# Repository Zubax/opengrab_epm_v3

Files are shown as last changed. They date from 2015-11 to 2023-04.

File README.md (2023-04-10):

OpenGrab EPM v3
===============

⚠⚠ **OpenGrab EPM v3 is no longer in production. Please use [Zubax EPM](https://zubax.com/products/epm) as a replacement.** ⚠⚠

-----

OpenGrab EPM v3 is an electropermanent magnet, combining the advantages of electro and permanent magnets.
It has been developed by [NicaDrone](http://nicadrone.com) in collaboration with [Zubax Robotics](http://zubax.com).

Useful links:

* [**PRODUCT DOCUMENTATION**](https://kb.zubax.com/x/eoAh)
* [HARDWARE SOURCES](https://tools.upverter.com/eda/#designId=1dada3422c772add)
* [SUPPORT FORUM](http://forum.zubax.com)

## Building the firmware

### Prerequisites

* Python 2.7+ or Python 3.2+
* ARM GCC Embedded 4.9+

### Building

After cloning this repository, execute the following:

```bash
git submodule update --init --recursive
cd firmware
make -j8
```

The build outputs will be available in the directory `build/`.

## Flashing the firmware

### Useful info

* If you do not cycle the EPM you cannot get zapped.
* Don't zap your computer it will not survive.
* HV section to avoid touching during debug, see fig. 1.
* Solder Jumper settings see fig. 1 and 2.

#### V3 Rev 4B and earlier
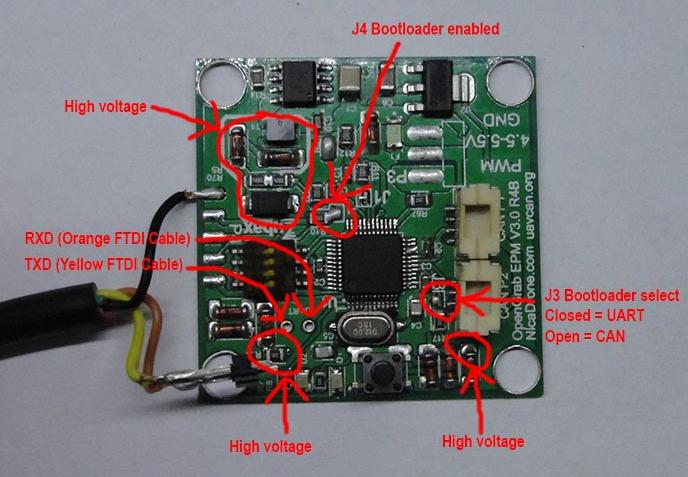
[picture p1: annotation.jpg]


#### V3 Rev 5C
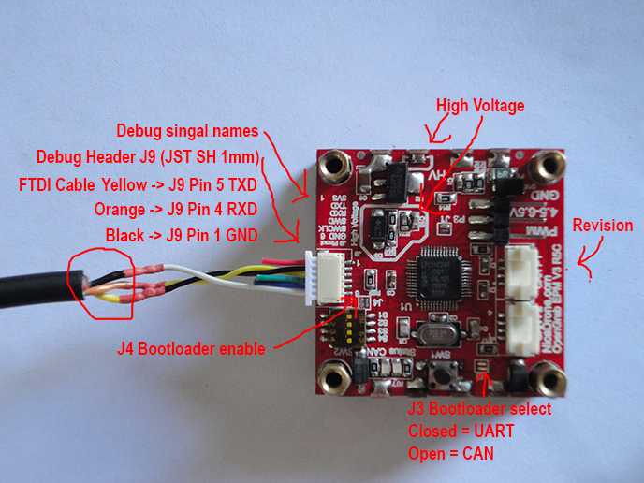
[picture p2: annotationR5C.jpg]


### Via UART

#### Connecting USB-UART adapter

FTDI cable is the recommended USB-UART adapter.
5 V and 3.3 V FTDI cables work fine, 3.3 V is recommended.
Use the following pinout when connecting:

Wire    | Signal
--------|--------
Orange  | RXD
Yellow  | TXD
Black   | GND

#### Flashing with NXP Flash Magic (simplest method)

Get the flashing tool from <http://www.flashmagictool.com/>.
Start the tool, then configure it as follows:

Parameter       | Value
----------------|------------------------------------
Select Device   | LPC11C24/301
Baud rate       | 115200
Interface       | ISP
Oscilator       | 12 MHz
File            | Prebuilt `.hex` available [here](https://files.zubax.com/products/com.zubax.opengrab_epm_v3/) **

1. Connect the USB-UART adapter.
2. Close J3 to select serial bootloader.
3. Close J4 to force the LPC to start the bootloader.
4. Power up the board.
5. Run the flashing tool.

** `.hex` is also created in the build output directory `firmware/build` or a `.hex` file can be created from `.bin`:

```bash
arm-none-eabi-objcopy -I binary -O ihex firmware.bin out.hex
```

### Via DroneCode Probe

[DroneCode Probe](https://kb.zubax.com/x/iIAh) is a generic JTAG / SWD + UART console adapter
compatible with most ARM Cortex based designs and in particular with hardware maintained by the
[DroneCode project](http://dronecode.org).

In order to flash the board using this tool, simply connect the debugger and execute the script
`blackmagic_flash.sh`.

### Via [8devices USB2CAN](http://www.8devices.com/usb2can) and embedded CAN bootloader

Note to Windows users: In order to use USB2CAN in a VM the drivers have to be installed on the host and driver
signature enforcement has to be disabled in some versions of Windows.

Register the CAN interface with SocketCAN:

```bash
sudo ip link set can0 up type can bitrate 100000 sample-point 0.875
```

Uploading binary using LPC11 embedded CAN bootloader:

```bash
tools/drwatson/lpc11c00_can_bootloader.py can0 firmware/build/firmware.bin
```

## Licenses

### Firmware

Copyright (C) 2015  Zubax Robotics <info@zubax.com>

This program is free software: you can redistribute it and/or modify
it under the terms of the GNU General Public License as published by
the Free Software Foundation, either version 3 of the License, or
(at your option) any later version.

This program is distributed in the hope that it will be useful,
but WITHOUT ANY WARRANTY; without even the implied warranty of
MERCHANTABILITY or FITNESS FOR A PARTICULAR PURPOSE.  See the
GNU General Public License for more details.

You should have received a copy of the GNU General Public License
along with this program.  If not, see <http://www.gnu.org/licenses/>.

### Hardware

The hardware sources are distributed under the terms of
[CC BY-SA 4.0](https://creativecommons.org/licenses/by-sa/4.0/).

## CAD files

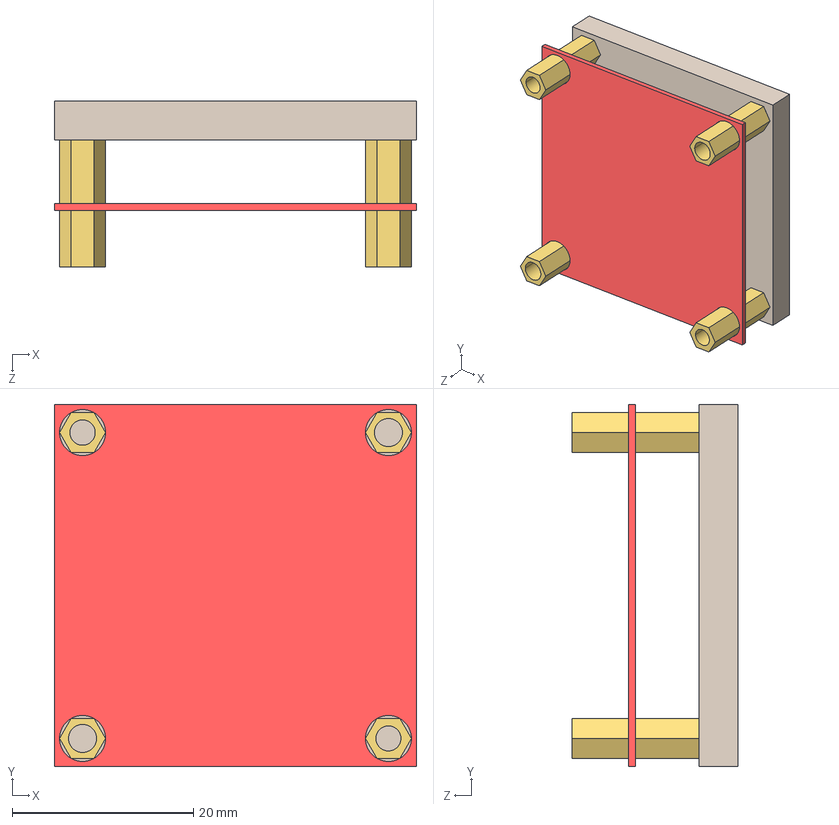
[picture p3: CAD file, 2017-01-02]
hardware/EPM_V3_Model.STEP
40.0 x 40.0 x 18.3 mm

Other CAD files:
hardware/EPM_V3_Model.IGS
hardware/EPM_V3_Model.SLDPRT

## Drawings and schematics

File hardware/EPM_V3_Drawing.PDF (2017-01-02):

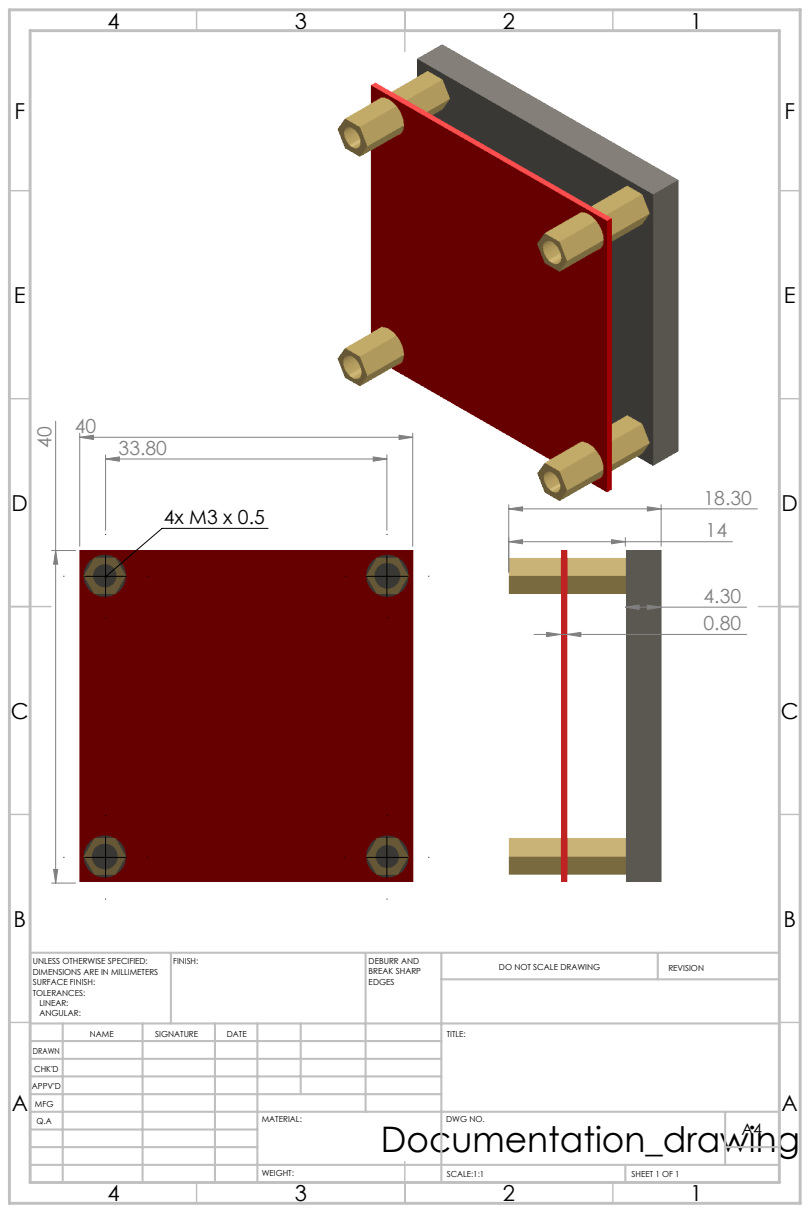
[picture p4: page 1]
FINISH:; DEBURR AND; BREAK SHARP; DO NOT SCALE DRAWING; REVISION; SCALE:1:1; SHEET 1 OF 1

UNLESS OTHERWISE SPECIFIED:
DIMENSIONS ARE IN MILLIMETERS
SURFACE FINISH:
TOLERANCES:
LINEAR:
ANGULAR:

NAME | SIGNATURE | DATE | | | | TITLE:

DRAWN
CHK'D
APPV'D
MFG
Q.A | | | | MATERIAL: Documentation_drawing | DWG NO. | A4

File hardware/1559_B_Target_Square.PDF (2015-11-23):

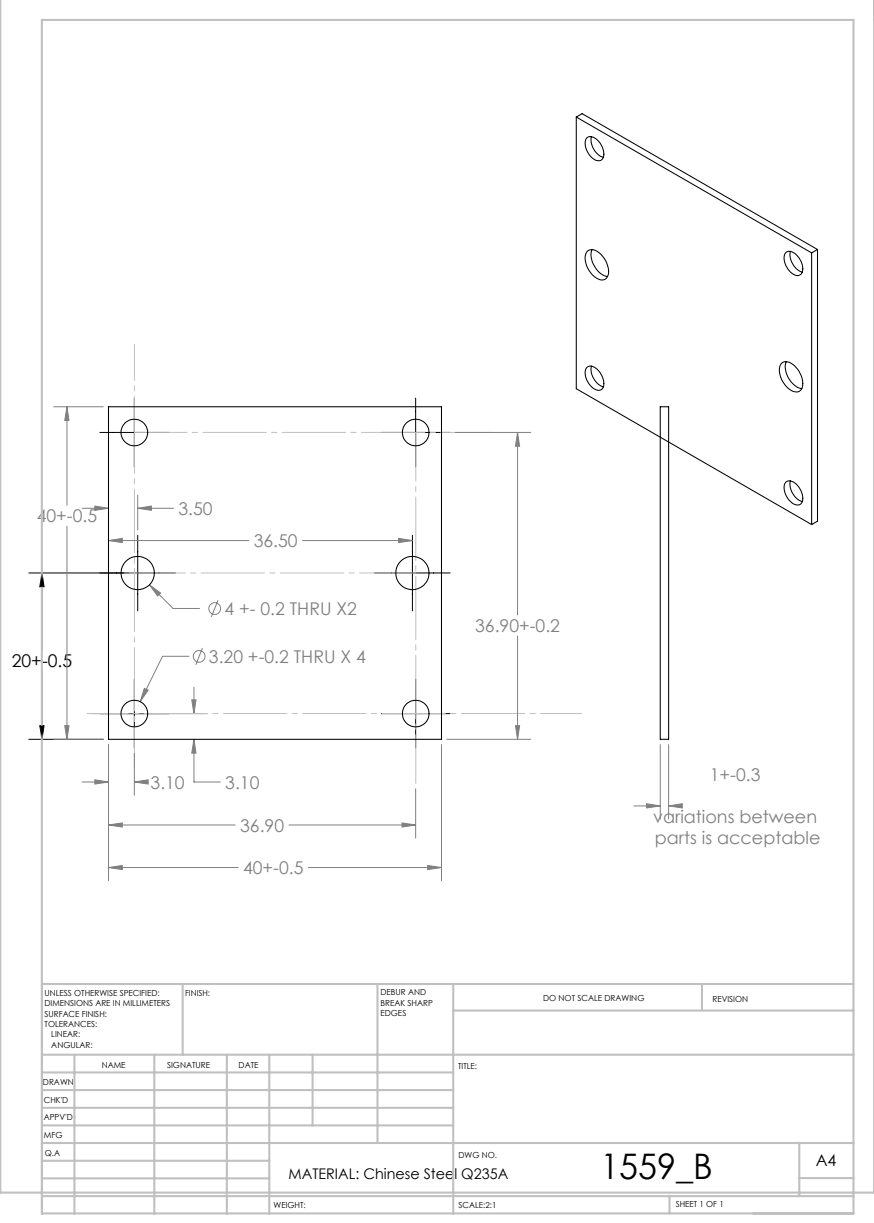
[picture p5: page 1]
3.20 +-0.2 THRU X 4; 4 +- 0.2 THRU X2; SCALE:2:1; SHEET 1 OF 1; DO NOT SCALE DRAWING; REVISION; DEBUR AND BREAK SHARP; UNLESS OTHERWISE SPECIFIED:; FINISH:

variations between
parts is acceptable

DIMENSIONS ARE IN MILLIMETERS
SURFACE FINISH:
TOLERANCES:
LINEAR:
ANGULAR:

NAME | SIGNATURE | DATE | | | | TITLE:

DRAWN
CHK'D
APPV'D
MFG
Q.A | | | | MATERIAL: Chinese Steel Q235A | 1559_B WEIGHT: DWG NO. | A4

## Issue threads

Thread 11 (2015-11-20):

Funky behavior when UAVCAN and PWM or button is used at the same time

ctech4285, 2015-11-20:
Temporary fix: Don't use CAN and PWM together,

PWM should be ignored when CAN is being used.

The CAN command is being send over and over again and the receiver only response to a change in command.
This is the typical way to use CAN bus - the same state is being published at a fixed rate or when it changes
This allows to ensure consistency even if the receiving node restarts

There seems to be a bug in somewhere as well....

pavel-kirienko, 2016-02-01:
Closing because we've already discussed that the device cannot accept multiple contradictory inputs at the same time.

Closed 2016-02-01.

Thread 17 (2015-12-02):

Command rate limiting not working when going on->off->on->off.....

ctech4285, 2015-12-02:

pavel-kirienko, 2015-12-02:
I understood that rate limiting is only needed if the goal does not change.

Remove `magnet_is_on` condition from https://github.com/Zubax/opengrab_epm_v3/blob/master/firmware/src/magnet/magnet.cpp#L194 and https://github.com/Zubax/opengrab_epm_v3/blob/master/firmware/src/magnet/magnet.cpp#L213

pavel-kirienko, 2015-12-03:
Is it fixed now?

ctech4285, 2015-12-03:
I can see now why you did it this way. Now a user has to wait like 3 seconds before going from turn on -> turn off...
Let me see what I can cock up

pavel-kirienko, 2016-02-01:
Still relevant?

Closed 2016-02-01.

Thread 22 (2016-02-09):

Vin measurement incorrect after boot

ctech4285, 2016-02-09:
make PRODROPPER=1

First time after boot when Vin is measured it returns 5000ish mV instead of 12000ish. ACD pin V is correct at this time at around 1000mV.

This commit has the syslog print out to reproduce

https://github.com/Zubax/opengrab_epm_v3/tree/pro_epm

pavel-kirienko, 2016-02-09:
This is because of averaging: https://github.com/Zubax/opengrab_epm_v3/blob/master/firmware/src/sys/board.cpp#L471.

We can either add initialization of the previous sample on first measurement, or we can remove averaging completely. We probably should remove it, it's wonky.

ctech4285, 2016-02-09:
Let's leave it in and call getSupplyVoltageInMillivolts a few times after boot? I am worried about introducing sporadic noise

pavel-kirienko, 2016-02-09:
No, we must not call it multiple times after boot because that creates a leaky abstraction. We can do this, right after `x` is computed:

```c++
if (old_value == 0)  // If old value is uninitialized, the result will be half of the real value
{
    x *= 2;
}
```

Closed 2016-02-11.

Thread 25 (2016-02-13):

Migrate to JST GH

pavel-kirienko, 2016-02-13:
References:
- http://www.digikey.com/product-detail/en/SM04B-GHS-TB(LF)(SN)%3B-/455-1566-1-ND/807834
- http://uavcan.org/Specification/8._Hardware_design_recommendations/#physical-connector-definition
- https://github.com/PX4/Hardware/issues/18

ctech4285, 2016-02-13:
This is going into PCB Rev6 then

ctech4285, 2016-11-07:
Done

Closed 2016-11-07.

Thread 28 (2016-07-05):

Customer was able to kill his EPM when turning on constantly

ctech4285, 2016-07-05:
There are some variations on the saturation current of T1 between parts

Reevalute using a smaller PTC fuse, fuse should pop before T1 gets damaged

Increasing minimum command interval

ctech4285, 2016-08-04:
cleaner implementation of better cycle limiting addressed this #34

Closed 2016-08-04.

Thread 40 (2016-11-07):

ADC seems to hickup every now and then

ctech4285, 2016-11-07:
It seems that it miss read input or output voltage, triggers an error

pavel-kirienko, 2016-11-07:
Please provide more info; the description you provided is insufficient. How exactly the misreading happens? How frequently? What output is produced and what output is expected? What error is triggered?

ctech4285, 2016-11-08:
Problem found, external ADC capacitor lags behind the main capacitor voltage.

https://github.com/Zubax/opengrab_epm_v3/blob/master/firmware/src/magnet/magnet.cpp#L262

Closed 2016-11-08.

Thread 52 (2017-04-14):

Catastrophic failure mode possible on different hardware

ctech4285, 2017-04-14:
Force 1 second delay when power stage misfires. Misfire = main capacitor is not  discharged after firing

It is possible on different hardware that the holding current is reached. Via the cathode pull down resistor on the power stage
It cause the Thyristor to stay on for up to 1 second. Subsequently firing its lower pair will cause the two thyristors to eat to much power and fail as short.

I'll take care of it before we change out the thyristors for the next rev

pavel-kirienko, 2017-04-22:
Please keep us posted. Let me know if any software changes are necessary.

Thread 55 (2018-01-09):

J9 Pin numbers in documentation pictures are incorrect

ctech4285, 2018-01-09:
https://github.com/Zubax/opengrab_epm_v3/raw/master/annotationR5C.jpg

Pin numbers on the PCB are correct; Pin number on the picture are incorrect

ctech4285, 2018-02-05:
User reports silkscreen label or the documentation is wrong. Pins 1-6 on J9 are labelled in the wrong order.

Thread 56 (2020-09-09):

Link to the hardware sources is broken.

nophead, 2020-09-09:
The title says it all.

pavel-kirienko, 2020-09-09:
@ctech4285 do we have any hope of fixing it?

nophead, 2020-09-10:
Is there any other source for the component positions. I want to 3D print an enclosure, so I need to know where the connectors, button, LEDs and switches are located.

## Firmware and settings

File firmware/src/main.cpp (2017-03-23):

/*
 * OpenGrab EPM - Electropermanent Magnet
 * Copyright (C) 2015  Zubax Robotics <info@zubax.com>
 *
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
 * Author: Pavel Kirienko <pavel.kirienko@zubax.com>
 *         Andreas Jochum <andreas@nicadrone.com>
 */

#include <cstdio>
#include <algorithm>
#include <sys/board.hpp>
#include <uavcan_lpc11c24/uavcan_lpc11c24.hpp>
#include <uavcan/equipment/hardpoint/Command.hpp>
#include <uavcan/equipment/hardpoint/Status.hpp>
#include <uavcan/protocol/dynamic_node_id_client.hpp>
#include <magnet/magnet.hpp>

namespace
{

static constexpr unsigned NodeMemoryPoolSize = 2800;

uavcan::Node<NodeMemoryPoolSize>& getNode()
{
    static uavcan::Node<NodeMemoryPoolSize> node(uavcan_lpc11c24::CanDriver::instance(),
                                                 uavcan_lpc11c24::SystemClock::instance());
    return node;
}

struct HwConfig
{
    std::uint8_t hardpoint_id = 0;
    bool use_hardpoint_id_as_node_id = false;

    static constexpr std::uint8_t NodeIDOffset = 100;
};

const HwConfig getHwConfig()
{
    static bool first = true;
    static HwConfig cfg;

    if (first)
    {
        first = false;
        const auto x = board::readDipSwitch();
        cfg.hardpoint_id = x & ((1 << (board::DipSwitchBits - 1)) - 1);
        cfg.use_hardpoint_id_as_node_id = (x >> (board::DipSwitchBits - 1)) != 0;
    }

    return cfg;
}

void callPollAndResetWatchdog()
{
    board::resetWatchdog();

    /*
     * Status LED update
     */
    const auto ts = board::clock::getMonotonic();

    static board::MonotonicTime led_update_deadline = ts;
    static bool led_status = false;
    static bool boot = true;
    static bool first_time_led_update = true;

    /*
     * LED DIP test after boot
     */
    if (boot)
    {
        boot = !boot;
        if(board::readDipSwitch() == 0)
        {
            board::setStatusLed(true);
            board::setCanLed(true);
            led_update_deadline += board::MonotonicDuration::fromMSec(500);
        }
    }

    if (ts >= led_update_deadline)
    {
        if(first_time_led_update)           // Turn off CAN status
        {
            board::setCanLed(false);
            first_time_led_update = !first_time_led_update;
        }
        led_status = !led_status;
        board::setStatusLed(led_status);

        if (led_status)
        {
            led_update_deadline += board::MonotonicDuration::fromMSec(50);
        }
        else
        {
            led_update_deadline += board::MonotonicDuration::fromMSec(
                (magnet::getHealth() == magnet::Health::Ok)      ? 950 :
                (magnet::getHealth() == magnet::Health::Warning) ? 500 : 100);
        }

        /* Debug
         * board::syslog("Vin = ", board::getSupplyVoltageInMillivolts(), " mV\r\n");
         * board::syslog("Vout = ", board::getOutVoltageInVolts(), " V\r\n");
         */
    }

    /*
     * PWM control update
     */
    const auto pwm = board::getPwmInput();
    if (pwm != board::PwmInput::NoSignal &&
        pwm != board::PwmInput::Neutral)
    {
        if (pwm == board::PwmInput::High)
        {
            magnet::turnOn(magnet::MinTurnOnCycles);
        }
        if (pwm == board::PwmInput::Low)
        {
            magnet::turnOff();
        }
    }

    /*
     * Button update
     */
    if (board::hadButtonPressEvent() || board::hadExternalButtonPressEvent() )
    {
        if (magnet::isTurnedOn())
        {
            magnet::turnOff();
        }
        else
        {
            magnet::turnOn(magnet::MinTurnOnCycles);
        }
    }

    /*
     * Magnet update
     */
    magnet::poll();
}

uavcan::NodeID performDynamicNodeIDAllocation()
{
    uavcan::DynamicNodeIDClient client(getNode());

    const int client_start_res = client.start(getNode().getHardwareVersion().unique_id);
    if (client_start_res < 0)
    {
        board::die();
    }

    while (!client.isAllocationComplete())
    {
        (void)getNode().spinOnce();
        callPollAndResetWatchdog();
    }

    return client.getAllocatedNodeID();
}

void fillNodeInfo()
{
    getNode().setName("com.zubax.opengrab_epm_v3");

    {
        uavcan::protocol::SoftwareVersion swver;

        swver.major = FW_VERSION_MAJOR;
        swver.minor = FW_VERSION_MINOR;
        swver.vcs_commit = GIT_HASH;
        swver.optional_field_flags = swver.OPTIONAL_FIELD_FLAG_VCS_COMMIT;

        getNode().setSoftwareVersion(swver);
    }

    {
        uavcan::protocol::HardwareVersion hwver;

        hwver.major = HW_VERSION_MAJOR;

        {
            board::UniqueID uid;
            board::readUniqueID(uid);
            std::copy(std::begin(uid), std::end(uid), std::begin(hwver.unique_id));
        }

        {
            board::DeviceSignature coa;
            if (board::tryReadDeviceSignature(coa))
            {
                std::copy(std::begin(coa), std::end(coa), std::back_inserter(hwver.certificate_of_authenticity));
            }
        }

        getNode().setHardwareVersion(hwver);
    }
}

void configureAcceptanceFilters()
{
    // These masks are specific for UAVCAN - we're using only extended data frames and nothing else.
    static constexpr auto CommonIDBits   = uavcan::CanFrame::FlagEFF;
    static constexpr auto CommonMaskBits = uavcan::CanFrame::FlagEFF |
                                           uavcan::CanFrame::FlagRTR |
                                           uavcan::CanFrame::FlagERR;

    static constexpr auto NodeIDShift     = 8;
    static constexpr auto MessageMaskBits = 0xFFFF80U;
    static constexpr auto ServiceIDBits   = 0x80U;
    static constexpr auto ServiceMaskBits = 0x7F80U;

    // Allocating a buffer large enough to fit all filters the application may need.
    static constexpr unsigned MaxFilterConfigs = 32;
    uavcan::CanFilterConfig filter_configs[MaxFilterConfigs];
    std::uint16_t filter_config_index = 0;

    // Building message filters.
    auto p = getNode().getDispatcher().getListOfMessageListeners().get();
    while (p != NULL)
    {
        filter_configs[filter_config_index].id =
            (static_cast<unsigned>(p->getDataTypeDescriptor().getID().get()) << NodeIDShift) | CommonIDBits;

        filter_configs[filter_config_index].mask = MessageMaskBits | CommonMaskBits;

        p = p->getNextListNode();

        filter_config_index++;
        if (filter_config_index >= std::min<unsigned>(MaxFilterConfigs,
                                                      uavcan_lpc11c24::CanDriver::instance().getNumFilters()))
        {
            board::die(); // Filter compaction algorithm defined in libuavcan is not used because of memory constraints
        }
    }

    // Adding one filter for unicast transfers - note that it's filtering on our Node ID.
    filter_configs[filter_config_index].id =
        ServiceIDBits | (static_cast<unsigned>(getNode().getNodeID().get()) << NodeIDShift) | CommonIDBits;
    filter_configs[filter_config_index].mask = ServiceMaskBits | CommonMaskBits;

    filter_config_index++;

    // Sending the configuration to the CAN driver.
    if (uavcan_lpc11c24::CanDriver::instance().configureFilters(filter_configs, filter_config_index) < 0)
    {
        board::die();
    }
}

void handleHardpointCommand(const uavcan::equipment::hardpoint::Command& msg)
{
    if (msg.hardpoint_id != getHwConfig().hardpoint_id)
    {
        return;
    }

    /*
     * The last command field is initialized at an impossible value in order to force a switch once
     * the first command is received. This will force the magnet into a known state.
     */
    static unsigned last_command = std::numeric_limits<unsigned>::max();

    if ((bool(msg.command) != magnet::isTurnedOn()) || (msg.command != last_command))
    {
        if (msg.command == 0)
        {
            magnet::turnOff();
        }
        else
        {
            magnet::turnOn(msg.command);
        }
    }

    // Oi moroz moroz ne moroz' mena
    last_command = msg.command; // Ne moroz' mena moigo kona
}

void publishHardpointStatus()
{
    static const auto Priority = uavcan::TransferPriority::MiddleLower;

    static uavcan::Publisher<uavcan::equipment::hardpoint::Status> pub(getNode());

    static bool initialized = false;
    if (!initialized)
    {
        initialized = true;
        pub.setPriority(Priority);
    }

    uavcan::equipment::hardpoint::Status msg;

    msg.hardpoint_id = getHwConfig().hardpoint_id;

    msg.payload_weight = std::numeric_limits<float>::quiet_NaN();
    msg.payload_weight_variance = std::numeric_limits<float>::infinity();

    msg.status = magnet::isTurnedOn() ? 1 : 0;

    (void)pub.broadcast(msg);
}

void updateUavcanStatus(const uavcan::TimerEvent&)
{
    publishHardpointStatus();

    switch (magnet::getHealth())
    {
    case magnet::Health::Ok:
    {
        getNode().setHealthOk();
        break;
    }
    case magnet::Health::Warning:
    {
        getNode().setHealthWarning();
        break;
    }
    default:
    {
        getNode().setHealthError();
        break;
    }
    }

    getNode().setVendorSpecificStatusCode(
        static_cast<std::uint16_t>(magnet::getStatusFlags() | ((board::getOutVoltageInVolts() >> 1) << 8)));
}

void updateCanLed(const uavcan::TimerEvent&)
{
    board::setCanLed(uavcan_lpc11c24::CanDriver::instance().hadActivity());
}

#if __GNUC__
__attribute__((noinline))
#endif
void init()
{
    board::syslog("Boot\r\n");
    board::syslog("FW built at ");
    board::syslog(__DATE__);
    board::syslog("\r\n");
    board::resetWatchdog();

    callPollAndResetWatchdog();

    /*
     * Configuring the CAN controller
     */
    std::uint32_t bit_rate = 0;
    while (bit_rate == 0)
    {
        bit_rate = uavcan_lpc11c24::CanDriver::detectBitRate(&callPollAndResetWatchdog);
    }
    board::syslog("Bitrate: ", bit_rate, "\r\n");

    if (uavcan_lpc11c24::CanDriver::instance().init(bit_rate) < 0)
    {
        board::die();
    }

    board::syslog("CAN init ok\r\n");

    callPollAndResetWatchdog();

    /*
     * Starting the node
     */
    fillNodeInfo();

    if (getNode().start() < 0)
    {
        board::die();
    }

    callPollAndResetWatchdog();

    /*
     * Starting the node and performing dynamic node ID allocation
     */
    if (getNode().start() < 0)
    {
        board::die();
    }

    /*
     * Initializing other libuavcan-related objects
     * Why reinterpret_cast<>() on function pointers? Try to remove it, or replace with static_cast. GCC is fun.   D:
     */
    static uavcan::TimerEventForwarder<void (*)(const uavcan::TimerEvent&)> can_led_timer(getNode());   // CAN LED tmr
    can_led_timer.setCallback(reinterpret_cast<decltype(can_led_timer)::Callback>(&updateCanLed));
    can_led_timer.startPeriodic(uavcan::MonotonicDuration::fromMSec(25));

    if (getHwConfig().use_hardpoint_id_as_node_id)
    {
        board::syslog("Node ID is fixed\r\n");
        getNode().setNodeID(static_cast<std::uint8_t>(getHwConfig().hardpoint_id + HwConfig::NodeIDOffset));
    }
    else
    {
        board::syslog("Node ID allocation...\r\n");
        getNode().setNodeID(performDynamicNodeIDAllocation());
    }

    board::syslog("Node ID ", getNode().getNodeID().get(), "\r\n");

    callPollAndResetWatchdog();

    /*
     * Initializing other libuavcan-related objects
     */
    static uavcan::TimerEventForwarder<void (*)(const uavcan::TimerEvent&)> update_timer(getNode());    // Status pub
    update_timer.setCallback(reinterpret_cast<decltype(update_timer)::Callback>(&updateUavcanStatus));
    update_timer.startPeriodic(uavcan::MonotonicDuration::fromMSec(500));

    static uavcan::Subscriber<uavcan::equipment::hardpoint::Command,                                    // Command sub
                              void (*)(const uavcan::equipment::hardpoint::Command&)> command_sub(getNode());
    if (command_sub.start(reinterpret_cast<decltype(command_sub)::Callback>(&handleHardpointCommand)) < 0)
    {
        board::die();
    }

    /*
     * Configuring the filters in the last order, when all subscribers are initialized.
     */
    configureAcceptanceFilters();
}

}

int main()
{
    init();

    getNode().setModeOperational();

    board::setStatusLed(false);

    board::syslog("Init OK\r\n");

    while (true)
    {
        const int res = getNode().spinOnce();
        if (res < 0)
        {
            board::syslog("Spin error ", res, "\r\n");
        }

        callPollAndResetWatchdog();
    }
}

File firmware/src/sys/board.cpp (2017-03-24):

/*
 * OpenGrab EPM - Electropermanent Magnet
 * Copyright (C) 2015  Zubax Robotics <info@zubax.com>
 *
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
 * Author: Pavel Kirienko <pavel.kirienko@zubax.com>
 *         Andreas Jochum <andreas@nicadrone.com>
 *
 * Board initialization for Olimex LPC11C24 and EPM hardware.
 */

#include "board.hpp"
#include <chip.h>
#include <cstdlib>
#include <cstring>
#include <numeric>
#include <cstdint>
#include <algorithm>
#include <array>
#include <uavcan_lpc11c24/clock.hpp>

#define PDRUNCFGUSEMASK 0x0000ED00
#define PDRUNCFGMASKTMP 0x000000FF

constexpr std::uint32_t OscRateIn = 12000000; ///< External crystal
constexpr std::uint32_t ExtRateIn = 0;

std::uint32_t SystemCoreClock = 12000000; ///< Initialized to default clock value, will be changed on init

namespace board
{
namespace
{

constexpr std::uint32_t TargetSystemCoreClock = 48000000;

constexpr unsigned AdcReferenceMillivolts = 3300;
constexpr unsigned AdcResolutionBits = 10;

constexpr unsigned PwmPortNum = 2;
constexpr unsigned PwmInputPinMask = 1U << 10;

#if BOARD_OLIMEX_LPC_P11C24
constexpr unsigned CanLedPortNum = 1;
constexpr unsigned CanLedPinMask = 1U << 11;
#else
constexpr unsigned CanLedPortNum = 2;
constexpr unsigned CanLedPinMask = 1U << 6;
#endif

constexpr unsigned StatusLedPortNum = 2;
constexpr unsigned StatusLedPinMask = 1U << 0;

constexpr unsigned ExternalButtonPortNum = 1;
constexpr unsigned ExternalButtonPinMask = 1U << 6;

constexpr unsigned PumpSwitchPortNum = 1;
constexpr unsigned PumpSwitchPinMask = (1U << 0) | (1U << 1) | (1U << 2) | (1U << 4);

constexpr unsigned MagnetCtrlPortNum = 2;

constexpr unsigned MagnetCtrlPinLeftLow   = 1U << 2;   // PIO2_2
constexpr unsigned MagnetCtrlPinRightHigh = 1U << 8;   // PIO2_8

constexpr unsigned MagnetCtrlPinRightLow  = 1U << 1;   // PIO2_1
constexpr unsigned MagnetCtrlPinLeftHigh  = 1U << 7;   // PIO2_7

constexpr unsigned DipSwitchPortNum = 3;
constexpr unsigned DipSwitchPinMask = 0b1111;

constexpr std::uint32_t PwmInputPeriodMinUSec = 500;
constexpr std::uint32_t PwmInputPeriodMaxUSec = 2500;
constexpr std::uint32_t PwmInputTimeoutUSec   = 100000;
static std::uint32_t pwm_input_pulse_usec;
static uavcan::MonotonicTime last_pwm_input_update_ts;

struct CriticalSectionLocker
{
    CriticalSectionLocker()
    {
        __disable_irq();
    }
    ~CriticalSectionLocker()
    {
        __enable_irq();
    }
};

struct PinMuxGroup
{
    const unsigned pin      : 8;
    const unsigned modefunc : 24;
};

/**
 * Note that output pins that must be initialized with low output level are configured with PULLDOWN.
 * This is a work around - the GPIO controller does not provide a deterministic way to set initial output value;
 * instead, once the DIR bit goes up, the output state will be determined by the input state at the moment when the
 * DIR bit was changed.
 * Refer to the chapter "12.3.1 GPIO data register" of the user manual for details.
 */
constexpr PinMuxGroup pinmux[] =
{
    // PIO0
    { IOCON_PIO0_11, IOCON_FUNC2 | IOCON_MODE_INACT | IOCON_ADMODE_EN |IOCON_OPENDRAIN_EN },    // Vout_ADC

    // PIO1
    { IOCON_PIO1_10, IOCON_FUNC1 | IOCON_MODE_INACT | IOCON_ADMODE_EN |IOCON_OPENDRAIN_EN },    // Vin_ADC

    { IOCON_PIO1_7,  IOCON_FUNC1 | IOCON_HYS_EN | IOCON_MODE_PULLUP },                          // UART_TXD
#if BOARD_OLIMEX_LPC_P11C24
    { IOCON_PIO1_11, IOCON_FUNC0 | IOCON_HYS_EN | IOCON_DIGMODE_EN },                           // CAN LED
#endif

    { IOCON_PIO1_0,  IOCON_FUNC1 | IOCON_MODE_PULLDOWN | IOCON_HYS_EN | IOCON_DIGMODE_EN },     // PUMP SW0
    { IOCON_PIO1_1,  IOCON_FUNC1 | IOCON_MODE_PULLDOWN | IOCON_HYS_EN | IOCON_DIGMODE_EN },     // PUMP SW1
    { IOCON_PIO1_2,  IOCON_FUNC1 | IOCON_MODE_PULLDOWN | IOCON_HYS_EN | IOCON_DIGMODE_EN },     // PUMP SW2
    { IOCON_PIO1_4,  IOCON_FUNC0 | IOCON_MODE_PULLDOWN | IOCON_HYS_EN | IOCON_DIGMODE_EN },     // PUMP SW4
    { IOCON_PIO1_6,  IOCON_FUNC0 | IOCON_HYS_EN | IOCON_MODE_PULLDOWN },                        // External Button

    // PIO2
    { IOCON_PIO2_0,  IOCON_FUNC0 | IOCON_HYS_EN | IOCON_MODE_PULLDOWN },                        // Status LED
#if !BOARD_OLIMEX_LPC_P11C24
    { IOCON_PIO2_6,  IOCON_FUNC0 },                                                             // CAN LED
#endif

    { IOCON_PIO2_10, IOCON_FUNC0 | IOCON_HYS_EN | IOCON_MODE_PULLDOWN },                        // PWM

    { IOCON_PIO2_1,  IOCON_FUNC0 | IOCON_HYS_EN | IOCON_MODE_PULLDOWN | IOCON_DIGMODE_EN },     // CTRL3
    { IOCON_PIO2_7,  IOCON_FUNC0 | IOCON_HYS_EN | IOCON_MODE_PULLDOWN | IOCON_DIGMODE_EN },     // CTRL2

    { IOCON_PIO2_2,  IOCON_FUNC0 | IOCON_HYS_EN | IOCON_MODE_PULLDOWN | IOCON_DIGMODE_EN },     // CTRL1
    { IOCON_PIO2_8,  IOCON_FUNC0 | IOCON_HYS_EN | IOCON_MODE_PULLDOWN | IOCON_DIGMODE_EN },     // CTRL4
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

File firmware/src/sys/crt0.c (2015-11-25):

/*
 * OpenGrab EPM - Electropermanent Magnet
 * Copyright (C) 2015  Zubax Robotics <info@zubax.com>
 *
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
 * Author: Pavel Kirienko <pavel.kirienko@zubax.com>
 */

typedef void (*funptr_t)(void);

#define fill32(start, end, filler) {   \
    unsigned *p1 = start;              \
    const unsigned * const p2 = end;   \
    while (p1 < p2)                    \
        *p1++ = filler;                \
}

extern const unsigned _etext;

extern unsigned _data;
extern unsigned _edata;

extern unsigned _bss;
extern unsigned _ebss;

extern funptr_t __init_array_start;
extern funptr_t __init_array_end;

__attribute__((noreturn))
extern int main(void);

extern void SystemInit(void);

#pragma GCC optimize 1

/**
 * Prototypes for the functions below
 */
void Reset_Handler(void);
void Default_Handler(void);
void NMI_Handler(void);
void HardFault_Handler(void);
void SVC_Handler(void);
void PendSV_Handler(void);
void SysTick_Handler(void);

/**
 * Firmware entry point
 */
__attribute__((naked, noreturn))
void Reset_Handler(void)
{
    // Data section
    {
        const unsigned* tp = &_etext;
        unsigned* dp = &_data;
        while (dp < &_edata)
        {
            *dp++ = *tp++;
        }
    }

    // BSS section
    fill32(&_bss, &_ebss, 0);

    SystemInit();

    // Constructors
    {
        funptr_t* fpp = &__init_array_start;
        while (fpp < &__init_array_end)
        {
            (*fpp)();
            fpp++;
        }
    }

    (void)main();

    while (1) { }
}

/**
 * Default handlers
 */
__attribute__((weak))
void Default_Handler(void)
{
    while(1) { }
}

__attribute__((weak))
void NMI_Handler(void)
{
    while(1) { }
}

__attribute__((weak))
void HardFault_Handler(void)
{
    while(1) { }
}

__attribute__((weak))
void SVC_Handler(void)
{
    while(1) { }
}

__attribute__((weak))
void PendSV_Handler(void)
{
    while(1) { }
}

__attribute__((weak))
void SysTick_Handler(void)
{
    while(1) { }
}

/**
 * Default vectors for LPC11C24, to be overriden by the firmware as needed
 */
#define ALIAS(f) __attribute__ ((weak, alias (#f)))

void CAN_IRQHandler(void) ALIAS(Default_Handler);
void SSP1_IRQHandler(void) ALIAS(Default_Handler);
void I2C_IRQHandler(void) ALIAS(Default_Handler);
void TIMER16_0_IRQHandler(void) ALIAS(Default_Handler);
void TIMER16_1_IRQHandler(void) ALIAS(Default_Handler);
void TIMER32_0_IRQHandler(void) ALIAS(Default_Handler);
void TIMER32_1_IRQHandler(void) ALIAS(Default_Handler);
void SSP0_IRQHandler(void) ALIAS(Default_Handler);
void UART_IRQHandler(void) ALIAS(Default_Handler);
void ADC_IRQHandler(void) ALIAS(Default_Handler);
void WDT_IRQHandler(void) ALIAS(Default_Handler);
void BOD_IRQHandler(void) ALIAS(Default_Handler);
void PIOINT3_IRQHandler(void) ALIAS(Default_Handler);
void PIOINT2_IRQHandler(void) ALIAS(Default_Handler);
void PIOINT1_IRQHandler(void) ALIAS(Default_Handler);
void PIOINT0_IRQHandler(void) ALIAS(Default_Handler);
void WAKEUP_IRQHandler(void) ALIAS(Default_Handler);

/**
 * Refer to the linker script
 */
extern void __stack_end(void);

/**
 * Vector table for LPC11Cxx
 * Must be explicitly defined 'used', otherwise LTO optimizer will discard it.
 */
__attribute__ ((used, section("vectors")))
void (* const VectorTable[64])(void) =
{
    __stack_end,                            // The initial stack pointer
    Reset_Handler,                          // The reset handler
    NMI_Handler,                            // The NMI handler
    HardFault_Handler,                      // The hard fault handler
    0,                                      // Reserved
    0,                                      // Reserved
    0,                                      // Reserved
    0,                                      // Reserved
    0,                                      // Reserved
    0,                                      // Reserved
    0,                                      // Reserved
    SVC_Handler,                            // SVCall handler
    0,                                      // Reserved
    0,                                      // Reserved
    PendSV_Handler,                         // The PendSV handler
    SysTick_Handler,                        // The SysTick handler

    WAKEUP_IRQHandler,                      // PIO0_0  Wakeup
    WAKEUP_IRQHandler,                      // PIO0_1  Wakeup
    WAKEUP_IRQHandler,                      // PIO0_2  Wakeup
    WAKEUP_IRQHandler,                      // PIO0_3  Wakeup
    WAKEUP_IRQHandler,                      // PIO0_4  Wakeup
    WAKEUP_IRQHandler,                      // PIO0_5  Wakeup
    WAKEUP_IRQHandler,                      // PIO0_6  Wakeup
    WAKEUP_IRQHandler,                      // PIO0_7  Wakeup
    WAKEUP_IRQHandler,                      // PIO0_8  Wakeup
    WAKEUP_IRQHandler,                      // PIO0_9  Wakeup
    WAKEUP_IRQHandler,                      // PIO0_10 Wakeup
    WAKEUP_IRQHandler,                      // PIO0_11 Wakeup
    WAKEUP_IRQHandler,                      // PIO1_0  Wakeup

    CAN_IRQHandler,                         // C_CAN Interrupt
    SSP1_IRQHandler,                        // SPI/SSP1 Interrupt
    I2C_IRQHandler,                         // I2C0
    TIMER16_0_IRQHandler,                   // CT16B0 (16-bit Timer 0)
    TIMER16_1_IRQHandler,                   // CT16B1 (16-bit Timer 1)
    TIMER32_0_IRQHandler,                   // CT32B0 (32-bit Timer 0)
    TIMER32_1_IRQHandler,                   // CT32B1 (32-bit Timer 1)
    SSP0_IRQHandler,                        // SPI/SSP0 Interrupt
    UART_IRQHandler,                        // UART0

    0,                                      // Reserved
    0,                                      // Reserved

    ADC_IRQHandler,                         // ADC   (A/D Converter)
    WDT_IRQHandler,                         // WDT   (Watchdog Timer)
    BOD_IRQHandler,                         // BOD   (Brownout Detect)
    0,                                      // Reserved
    PIOINT3_IRQHandler,                     // PIO INT3
    PIOINT2_IRQHandler,                     // PIO INT2
    PIOINT1_IRQHandler,                     // PIO INT1
    PIOINT0_IRQHandler,                     // PIO INT0

    0,
    0,
    0,
    0,
    0,
    0,
    0,
    0,
    0,
    0,
    0,
    0,
    0,
    0,
    0,
    0
};

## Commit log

2015-05-29 Blinking LEDs
2015-06-03 Fixed charbe pump switch interface
    [board.cpp]
2015-06-03 LPCWare ADC driver
2015-06-03 Button test
2015-06-03 board: naming fix, bug fix
    [board.cpp]
2015-06-03 board::delayUSec() with a test
2015-06-04 UART test
2015-06-04 Button debug code
2015-06-06 Fixed GPIO config for demoboard
    [board.cpp]
2015-06-06 UART driver fix
2015-06-06 Reworked delay function, simple meander test
    [board.cpp, main.cpp]
2015-06-06 Pin synchronization
2015-06-11 ADC driver, supply voltage measurement and simple test
2015-06-11 PWM input
2015-06-16 individual control pumpswitch
2015-06-18 Charge pump is fixed
    [board.cpp, main.cpp]
2015-07-29 Updated switch GPIO
2015-08-01 Clean up, Mosftet drive is fixed Charging function needs work Status LED blink is a little bit broken
    [board.cpp, main.cpp]
2015-08-02 Fixing charger implementation
2015-08-02 added charger class, long long to char conversion function moved to util.cpp
2015-08-03 Build fix & minor refactoring
    [charger.cpp, main.cpp]
2015-08-17 ADC_Vin calibrated
2015-08-17 charger undervoltage overvoltage lock out
2015-08-17 Charger is working with over time protection
2015-09-01 Turn off working, worst case holding force when off 5N, needs a bit of calibrating Tested 2000 cycles
2015-09-01 PWM turn on / off added duty cycle limted to prevent overheating
    [main.cpp]
2015-10-25 Minor cleanup; some code has been moved into the board namespace
2015-10-25 DIP switch read function
2015-10-25 Acceptance filter configuration
2015-10-28 Issue fix: Lots of magic numbers in voltage measurement functions #4
    x += 650; //Poor man's optimizatin to not unintegerify the math, it's within 100mV -
    [board.cpp, charger.cpp]
2015-10-29 IRQ disabled for ~50us in charger instead of 1ms.
2015-10-29 Device signature support
2015-10-29 Minor renaming and commenting in board::
2015-10-29 minor changes here and there, first attempt at running the charger dynamicly
    The cycle function off time is to long even with accessing the GPIO's directly
2015-10-30 board::runPump() function
2015-10-30 runPump() fixed and moved to RAM
    [board.cpp]
2015-10-31 calculating on time for the pump seems to work fine off time math is wrong needs fixing
    [board.cpp, charger.cpp]
2015-10-31 Off time math should be good now The peak current is proably too high, on time needs some calibratoin Should be almost ready to go
    [charger.cpp]
2015-11-02 Charger::run() cleaned up and a lot nicer
    unsigned on_time=((5000000/(supply_voltage_mV-500))/104); needs fixing
    formating as well needs some clean up
    chrg.set(Uout);
    chrg.run();
    bool isdone();
    [charger.cpp]
2015-11-03 harger is optimized for speed and runs fine, rippel after fuse is a bit much charge time: ~180ms @ Uin =5V
    source current is still within limits
2015-11-03 minior fix to charger, first attempt at finite state magnetOff()
    [charger.cpp]
2015-11-04 magnet turns off faster by skipping the first 3 cycles if the the magnet was not completly on some minor stuff
2015-11-18 PWM fix
2015-11-18 Async charger
2015-11-18 LED indication
2015-11-18 LED update logic decoupled from uavcan
2015-11-18 Magnet tate reporting
2015-11-18 Button control
2015-11-19 UAVCAN command handling fixed
    [main.cpp]
2015-11-19 Button logic fix
2015-11-19 Increased button jitter suppression threshold
    [board.cpp]
2015-11-19 Vin minimum for the charger to run is set to 4300mV Vin lower limit is 4500mV for pump timing calculation
    board::runPump on/off times is wrong now. Tempoarly fixed by asuming inductor is 5uh
    [charger.cpp]
2015-11-19 DIP switch handling fix, also fixes #10
    [board.cpp, main.cpp]
2015-11-19 added DIP switch configuration to readme..
2015-11-19 PWM handling without magic numbers
2015-11-19 Input voltage clamping moved to board::
2015-11-19 runPump timing seems to be ok again, unduing the temporary fix
    [charger.cpp]
2015-11-19 Charger restart logic fix
2015-11-19 Magnet init() removed because it was useless
2015-11-20 charger timing ajusted
2015-11-20 Skipping first 3 cycles when turning OFF if the magnet was already OFF
2015-11-20 Ignoring commands while switching is in progress; resolves #14
2015-11-23 Added dimensional drawings
    [EPM_V3.SLDPRT, EPM_V3_simple.SLDDRW]
2015-11-25 ajusted charger timing to account for variations in inductors
2015-11-27 Fixed unique ID reading
    [board.cpp]
2015-11-30 drwatson: printing jumper names together with MCU pin names; state of PIO0_3 is not enforced when starting the firmware
2015-12-01 added support for Prodropper charger magic souce, change in time out, change input voltage range
2015-12-01 Revert "Merge branch 'master' of https://github.com/Zubax/opengrab_epm_v3"
    This reverts commit 4af2478953bb52c9213c6436ae77ebfbfcc9ff4e, reversing
    changes made to 56d500986d248e2a33becabce97fc1346d07db53.
    [charger.cpp]
2015-12-01 Added C++ test app; Hardpoint status message now published with correctly initialized weight fields
    [main.cpp]
2015-12-16 small change to charger timing
2016-02-06 merged Prodropper branch make PRODROPPER=1 not working yet
    [charger.cpp, main.cpp]
2016-02-09 added cycle limit for all cases and debug print outs
2016-02-10 Adjusted config variables, added syslog print for low /high Vin conditions, fixed a bug in cycle limiting
    [charger.cpp]
2016-02-11 fixed missing end line character
    [charger.cpp]
2016-02-11 added dip switch test, not working
    [main.cpp]
2016-02-11 LED DIP test working
2016-02-17 Create Capacitor_test_report
2016-03-02 ADC calibration / debug
2016-03-04 Calibrated Vin sense < 2% error Reduce current consumtion to ~300mA RMS when Vin is <4.8V Makes EPM compatible with crappy power supplies such as PixHawk or cellphone chargers
    [board.cpp, charger.cpp, main.cpp]
2016-09-09 ADC vout averaging not working right needs fixing
    [board.cpp]
2016-09-09 ADC vout works
2016-09-10 U supply min measurment,...doesn't work
    [board.cpp, charger.cpp]
2016-09-10 Tracking supply voltage during switching is working now :D
2016-09-28 Print build date over UART at boot
2016-10-10 Flashing with NXP Flash Magic clarification
    settings added "Select Device LPC11C24/301"
2016-11-08 Measurment of main capacitor after discrage returned bad result sometimes, RC time constant of feed feedback is +- 1.5[ms]. Incresed settle time to 4[ms]
2017-01-01 Updated model and drawing, PDF, IGS and STEP
    [EPM_V3_Model.IGS, EPM_V3_Model.SLDPRT, EPM_V3_Model.STEP]
2017-02-05 Fixed typos and formatting
    [board.cpp]
2017-03-23 Added support for external button, RXD on J9
2017-03-24 Fixed ordering of pin definitions
    [board.cpp]
2017-06-29 decreasing Ip increases charger eff by 5% points
